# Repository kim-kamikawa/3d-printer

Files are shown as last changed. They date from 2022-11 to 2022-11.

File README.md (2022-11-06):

# 3D-Printer

## Overview

An Anet A8 3D printer was stripped of its controller board and its components connected to an Arduino Uno as shown in the following schematic.
Schematic

|Part ID|Part Name|Part Number||Part ID|Part Name|Part Number|
|---|---|---|---|---|---|---|
|C1|0.1uF|||U4|Stepper Driver|A4988|
|C2|0.1uF|||U5|Stepper Driver|A4988|
|C3|0.1uF|||U6|X-Axis Stepper|42SHDC3025-24B|
|C4|0.1uF|||U7|Y-Axis Stepper|42SHDC3025-24B|
|C5|0.1uF|||U8|Z-Axis Stepper|42SHDC3025-24B|
|C6|100uF|||U9|Z-Axis Stepper|42SHDC3025-24B|
|C7|100uF|||U10|Extruder Stepper|42SHDC3025-24B|
|C8|100uF|||U11|X-Min Stop|10T85|
|C9|100uF|||U12|Y-Min Stop|10T85|
|C10|10uF|||U13|Z-Min Stop|10T85|
|M1|IRF520|||U14|Power Module|BIQU-3D0109|
|R1|100k|||U15|Hot End|ANET-0029|
|U1|Arduino Uno|Arduino-A000066||U16|Thermistor|NTC 3960 100k|
|U2|Stepper Driver|A4988||U17|USB to Serial|OSEPP FTD-01|
|U3|Stepper Driver|A4988|

A STL file (cube.stl) was created of a 1.25-inch cube with 0.125-inch walls and a 1-inch by 0.125-inch opening on top. The STL was converted into g-code (cube.gcode) using Cura.

Knowing Repetier Host would be used to stream the g-code from a PC to the Arduino Uno, code was created for the Arduino Uno to receive g-code through its USART and parse the subset of g-code commands found in the g-code file.

The following g-codes from the file were implemented: G0 (rapid linear move), G1 (linear move), G28 (move to origin), and M109 (set extruder temperature and wait). In addition, M105 (get extruder temperature) was implemented to display the extruder’s temperature in Repetier Host. 

The following settings are hard-coded: units are in millimeters, all positioning is absolute, fans are always on and feed rate is constant. Since feed rate is constant, parameter ‘F’ is not used and, G0 and G1 are executed in the same manner. Additional restrictions to G0 and G1 functionalities are as follows: the length of filament to extrude is calculated (one pulse to the extruder stepper motor for every thirty pulses to the movement stepper motors), filament is only extruded if there is movement and the extruder direction is never reversed. Since the extruder direction is never reversed, the last two G1 lines in cube.gcode were commented out.

For M105 and M109, a one second timer triggers the ADC conversion of the thermistor voltage and the temperature is determined using the calculations found at https://www.allaboutcircuits.com/projects/measuring-temperature-with-an-ntc-thermistor/.

Controller_Hardware
Anet_A8
3D_Object

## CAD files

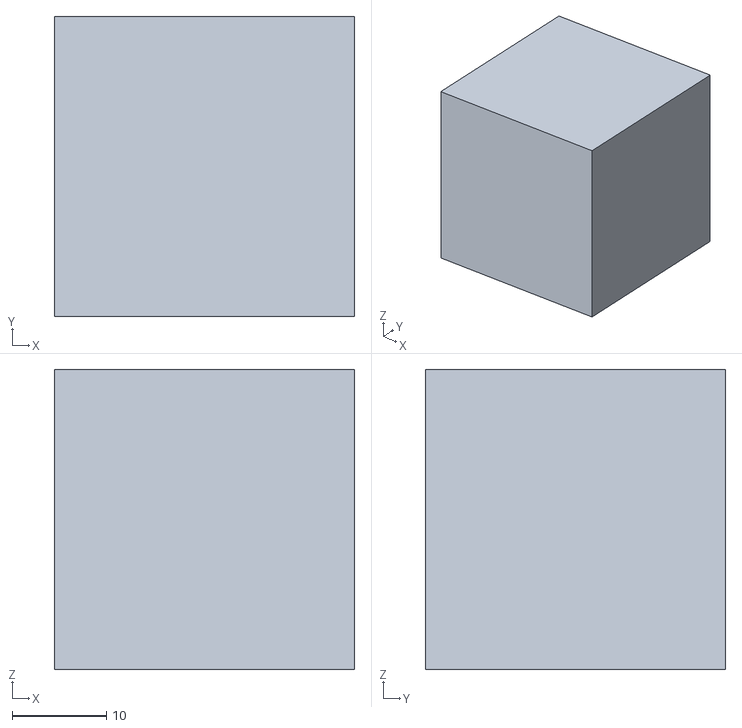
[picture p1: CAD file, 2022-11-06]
cube.STL
31.8 x 31.8 x 31.8

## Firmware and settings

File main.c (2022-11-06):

// Kim Lopez
// Embedded Controller Hardware Design
// ECE - 40001
// Final Project - 3D Printer
// 08-31-2018
  
#define F_CPU                   16000000
#define BAUD                    9600

#include <avr/io.h>
#include <avr/interrupt.h>
#include <util/delay.h>
#include <math.h>

#define BALANCE_RESISTOR 		100500.0
#define MAX_ADC 				1023.0
#define BETA 					3950.0
#define KELVIN_CONSTANT			273.15
#define ROOM_TEMP 				(25 + KELVIN_CONSTANT)
#define RESISTANCE_AT_ROOM_TEMP 100000

#define HOTEND_PWM_PIN          PB3

#define X_DIR_PIN               PD2   
#define X_STEP_PIN              PD3
#define X_HOME_PIN              PD4  
#define X_STEPS_PER_MM          100
 
#define Y_DIR_PIN               PD5 
#define Y_STEP_PIN              PD6
#define Y_HOME_PIN              PD7  
#define Y_STEPS_PER_MM          100

#define Z_DIR_PIN               PB0  
#define Z_STEP_PIN              PB1
#define Z_HOME_PIN              PB2   
#define Z_STEPS_PER_MM          400

#define E_DIR_PIN               PB4
#define E_STEP_PIN              PB5

#define PULSE_DURATION			200

struct Gcode {
	char letter;
	uint8_t number;
	uint8_t hasX;
	double x;
	uint8_t hasY;
	double y;
	uint8_t hasZ;
	double z;
	uint8_t hasE;
};

struct Position {
	double x;
	double y;
	double z;
};

volatile double hotEndTemperature = 0;
double hotEndSetting = 0;
int hotEndCounter = 0;

/*** SERIAL ***/

void initUSART() {
	// set baud rate
	unsigned int ubrr = F_CPU/16/BAUD-1;
	UBRR0H = (uint8_t)(ubrr>>8);
	UBRR0L = (uint8_t) ubrr;
	// enable receiver and transmitter
	UCSR0B |= (1<<RXEN0) | (1<<TXEN0);
	// 8-bit, no parity, 1 stop bit
	UCSR0C |= (1<<UCSZ01) | (1<<UCSZ00);   
}

uint8_t receiveUSART(void) {
	// wait for data to receive
	while (!(UCSR0A & (1<<RXC0)))
		;
	// return received byte
	return UDR0;
}

void transmitUSART(uint8_t data) {
	// wait for empty transmit buffer
	while (!(UCSR0A & (1<<UDRE0)))
		;
	// put data into buffer
	UDR0 = data;
}

/*** ADC ***/

void initADC() {
	/* initialize one second timer */
	// set CTC mode to match OCR1A (mode 4)
	TCCR1A = 0x0;
	TCCR1B = (1 << WGM12);
	// set prescaler to 1024 
	// => 16MHz/1024 = 15625Hz
	TCCR1B |= (1<<CS12) | (1<<CS10);
	// set compare match
	// => 15625 ticks = 1 second
	OCR1A = 15625;
	// initialize counter
	TCNT1 = 0;
	// enable Timer/Counter1 Compare Match A Interrupt
	TIMSK1 |= (1 << OCIE1A);

	/* initialize ADC */
	// set channel to pin A0 (PC0)
	// set voltage reference to AVcc
	ADMUX = (1<<REFS0);
	// set prescaler to 128
	// => 16MHz/128 = 125kHz
	// => ADC requires 50kHz-200kHz 
	ADCSRA |= (1<<ADPS2) | (1<<ADPS1) | (1<<ADPS0);
	// enable ADC interrupt
	ADCSRA |= (1<<ADIE);
	// turn off digital circuitry on A0
	DIDR0 |= (1<<ADC0D);
	// enable ADC
	ADCSRA |= (1<<ADEN);
	
	// enable global interrupt
	sei();
}

ISR(TIMER1_COMPA_vect) {
    // start ADC conversion
	ADCSRA |= (1<<ADSC);
}

ISR(ADC_vect) {
	// determine temperature of thermistor
	// https://www.allaboutcircuits.com/projects/measuring-temperature-with-an-ntc-thermistor/
	double rThermistor = BALANCE_RESISTOR * ((MAX_ADC / ADC) - 1);
	double tKelvin = (BETA * ROOM_TEMP) / (BETA + (ROOM_TEMP * log(rThermistor / RESISTANCE_AT_ROOM_TEMP)));
	hotEndTemperature = tKelvin - KELVIN_CONSTANT;
}

/*** HOT END ***/

void initHotEnd() {	
	/* initialize hot end PWM */
	// set pin 11 (PB3 & OC2A) as output
	DDRB |= (1<<HOTEND_PWM_PIN);
	// set fast PWM, top = 0xFF
	TCCR2A = (1<<WGM21) | (1<<WGM20);
	// set OC2A on compare match, clear OC2A at bottom
	TCCR2A |= (1<<COM2A1) | (1<<COM2A0);
	// set prescaler to 128
	// => 16MHz/128/256 = PWM frequency
	TCCR2B = (1<<CS22) | (1<<CS20);
	// set compare match
	// => 255 = 0% duty cycle (compare match ignored)
	// => 0 = 100% duty cycle
	OCR2A = 255;
	// initialize counter
	TCNT2 = 0;
}

/*** HOME SWITCHES and STEPPER MOTORS **/

void initHomeSwitches() {
	// home switches: set for input and pull-up resistor
	PORTD |= (1<<X_HOME_PIN) | (1<<Y_HOME_PIN);
	PORTB |= (1<<Z_HOME_PIN);
}

void initSteppers() {
	// set all steppers for output
	DDRD |= (1<<X_DIR_PIN) | (1<<X_STEP_PIN) | (1<<Y_DIR_PIN) | (1<<Y_STEP_PIN);
	DDRB |= (1<<Z_DIR_PIN) | (1<<Z_STEP_PIN) | (1<<E_DIR_PIN) | (1<<E_STEP_PIN);
	// set direction of stepper to extrude
	PORTB |= (1<<E_DIR_PIN);
}

/*** PARSING ***/

uint8_t getNumber(double *value) {
	
	uint8_t data;
	int num = 0;
	uint8_t multiplier = 1;
	double decimal = 0.0;
	uint8_t place = 0;
	
	// get integer part
	do {
		data = receiveUSART();
		switch (data) {
			case '+':
				break;
			case '-':
				multiplier = -1;
				break;
			case '0': case '1': case '2': case '3': case '4':
			case '5': case '6': case '7': case '8': case '9':
			    num = (num*10) + (data-'0');
				break;
			default:
				break;
		}
	} while (!((data == ' ') || (data == '.')));
	num *= multiplier;
	// get decimal part
	if (data == '.') {
		do {
			data = receiveUSART();
			switch (data) {
				case '0': case '1': case '2': case '3': case '4':
				case '5': case '6': case '7': case '8': case '9':
					decimal = (decimal*10.0) + (data-'0');
					place++;
					break;
				default:
					break;
			}
		} while (data != ' ');
		for (uint8_t x=0; x<place; x++)
			decimal *= 0.1;
	}
	
	*value = num + decimal;
	return data;
}

struct Gcode getCommand() {
	uint8_t data;
	struct Gcode command = {' ', 0, 0, 0.0, 0, 0.0, 0, 0.0, 0};
	
	// ignore line numbers
	do {
		
		data = receiveUSART(); 
	} while (data != ' ');
	
	// get letter
	data = receiveUSART();
		
	switch (data) {
		case 'G':
			data = receiveUSART();
			command.letter = 'G';			
			// get number
			switch (data) {
				case '0':
				case '1':
					command.number = 0;
					// G0: rapid linear move & G1: linear move
					data = receiveUSART();
					do {
						data = receiveUSART();
						
						// get parameters
						switch (data) {
							case 'X':
								// x coordinate in mm
								command.hasX = 1;
								data = getNumber(&(command.x));
								break;
							case 'Y':
								// y coordinate in mm
								command.hasY = 1;
								data = getNumber(&(command.y));
								break;
							case 'Z':
								// z coordinate in mm
								command.hasZ = 1;
								data = getNumber(&(command.z));
								break;
							case 'E':
								// e coordinate in mm
								command.hasE = 1;
								do {
									data = receiveUSART();
								} while (data != ' ');
								break;
							case 'F':
								// feedrate in mm per minute
								do {
									data = receiveUSART();
								} while (data != ' ');
								break;
							default:
								break;
						}
					} while (data != '*');
					break;
				case '2':
					data = receiveUSART();
					switch (data) {
						case '8':
							command.number = 28;
							// G28: move to origin
							data = receiveUSART();
							do {
								data = receiveUSART();
						
								// get parameters
								switch (data) {
									case 'X':
										// x coordinate in mm
										command.hasX = 1;
										data = getNumber(&(command.x));
										break;
									case 'Y':
										// y coordinate in mm
										command.hasY = 1;
										data = getNumber(&(command.y));
										break;
									case 'Z':
										// z coordinate in mm
										command.hasZ = 1;
										data = getNumber(&(command.z));
										break;
									default:
										break;
								}
							} while (data != '*');
							break;
						default:
							break;
					}
					break;
				default:
					break;
			}
			break; // 'G'
		case 'M':
			data = receiveUSART();
			command.letter = 'M';			
			// get number
			switch (data) {
				case '1':
					data = receiveUSART();
					switch (data) {
						case '0':
							data = receiveUSART();
							switch (data) {
								case '5':
									command.number = 105;
									// M105: get extruder temperature
									break;
								case '9':
									command.number = 109;
									// M109: set extruder temperature and wait
									data = receiveUSART();
									do {
										data = receiveUSART();
										switch (data) {
											case 'T':
												// temperature sensor number
												do {
													data = receiveUSART();
												} while (data != ' ');
												break;
											case 'S':
												// temperature value
												data = getNumber(&(hotEndSetting));
												break;
											default:
												break;
										}
									} while (data != '*');
									break;
								default:
									break;
							}
							break;
						default:
							break;
					}
					break;
				default:
					break;
			}
			break;
		default:
			break;
	}

	// ignore checksum
	do {
		data = receiveUSART(); 
	} while (!((data == '\r') || (data == '\n')));
	
	return command;
}
	
void sendOk() {
	// acknowledge receipt of command
	transmitUSART('o');
	transmitUSART('k');
	transmitUSART('\n');
}

/*** GCODE COMMANDS ***/

struct Position goLinear(struct Gcode gcode, struct Position currentPosition) {
	
	// G0: rapid linear move & G1: linear move
	int xSteps=0, ySteps=0, zSteps=0;
	struct Position position = currentPosition;

	if (gcode.hasX) {
		// compute steps
		xSteps = round((gcode.x - currentPosition.x) * X_STEPS_PER_MM);
		// set direction
		if (xSteps>0) {
			// go right
			PORTD |= (1<<X_DIR_PIN);
		}
		else {
			// go left
			PORTD &= ~(1<<X_DIR_PIN);
			xSteps *= -1;
		}
		// set ending position
		position.x = gcode.x;
	}
	if (gcode.hasY) {
		// compute steps
		ySteps = round((gcode.y - currentPosition.y) * Y_STEPS_PER_MM);
		// set direction
		if (ySteps>0) {
			// go front
			PORTD |= (1<<Y_DIR_PIN);
		}
		else {
			// go back
			PORTD &= ~(1<<Y_DIR_PIN);
			ySteps *= -1;
		}
		// set ending position
		position.y = gcode.y;
	}
	if (gcode.hasZ) {
		// compute steps
		zSteps = round((gcode.z - currentPosition.z) * Z_STEPS_PER_MM);
		// set direction
		if (zSteps>0) {
			// go up
			PORTB &= ~(1<<Z_DIR_PIN);
		}
		else {
			// go down
			PORTB |= (1<<Z_DIR_PIN);
			zSteps *= -1;
		}
		// set ending position
		position.z = gcode.z;
	}

	while (xSteps || ySteps || zSteps) {
		if (xSteps) {
			// send pulse to X-axis stepper
			PORTD |= (1<<X_STEP_PIN);
			xSteps--;
		}
		if (ySteps) {
			// send pulse to Y-axis stepper
			PORTD |= (1<<Y_STEP_PIN);
			ySteps--;
		}
		if (zSteps) {
			// send pulse to Z-axis steppers
			PORTB |= (1<<Z_STEP_PIN);
			zSteps--;
		}
		
		if (gcode.hasE) {
			// send pulse to extruder stepper
			// one extruder pulse for every 30 movement pulses
			if (hotEndCounter == 0) {
				PORTB |= (1<<E_STEP_PIN);
				hotEndCounter++;
			}
			else {
				if (hotEndCounter == 29)
					hotEndCounter = 0;
				else
					hotEndCounter++;
			}
		}
		
		// pulse duration
		_delay_us(PULSE_DURATION);
		
		// stop pulse
		PORTD &= ~(1<<X_STEP_PIN);
		PORTD &= ~(1<<Y_STEP_PIN);
		PORTB &= ~(1<<Z_STEP_PIN);	
		PORTB &= ~(1<<E_STEP_PIN);		
		
		// stop pulse duration
		_delay_us(PULSE_DURATION);
	} 
	
	return position;
}

struct Position goHome(struct Gcode gcode, struct Position currentPosition) {
	
	// G28: move to origin
	struct Position position = currentPosition;
	
	if (gcode.hasX) {
		// move X-axis stepper home
		PORTD &= ~(1<<X_DIR_PIN);
		while (bit_is_set(PIND, X_HOME_PIN)) {
			PORTD |= (1<<X_STEP_PIN);
			_delay_us(PULSE_DURATION);
			PORTD &= ~(1<<X_STEP_PIN);
			_delay_us(PULSE_DURATION);
		}
		// move X-axis stepper to zero
		PORTD |= (1<<X_DIR_PIN);
		for (int x=0; x<33*100; x++) {
			PORTD |= (1<<X_STEP_PIN);
			_delay_us(PULSE_DURATION);
			PORTD &= ~(1<<X_STEP_PIN);
			_delay_us(PULSE_DURATION);
		}
		position.x = 0;
	}
	if (gcode.hasY) {
		// move Y-axis stepper home
		PORTD &= ~(1<<Y_DIR_PIN);
		while (bit_is_set(PIND, Y_HOME_PIN)) {
			PORTD |= (1<<Y_STEP_PIN);
			_delay_us(PULSE_DURATION);
			PORTD &= ~(1<<Y_STEP_PIN);
			_delay_us(PULSE_DURATION);
		} 
		// move Y-axis stepper to zero
		PORTD |= (1<<Y_DIR_PIN);
		for (int x=0; x<4*100; x++) {
			PORTD |= (1<<Y_STEP_PIN);
			_delay_us(PULSE_DURATION);
			PORTD &= ~(1<<Y_STEP_PIN);
			_delay_us(PULSE_DURATION);
		}
		position.y = 0;
	}
	if (gcode.hasZ) {
		// move Z-axis stepper home
		PORTB |= (1<<Z_DIR_PIN);
		while (bit_is_set(PINB, Z_HOME_PIN)) {
			PORTB |= (1<<Z_STEP_PIN);
			_delay_us(PULSE_DURATION);
			PORTB &= ~(1<<Z_STEP_PIN);
			_delay_us(PULSE_DURATION);
		}
		// home is Z-axis origin
		position.z = 0;
	}

	return position;
}

void sendHotEndTemperature() {
	// M105: get extruder temperature
	transmitUSART('T');
	transmitUSART(':');
	transmitUSART('0' + ((int)hotEndTemperature / 100)); 
	transmitUSART('0' + (((int)hotEndTemperature / 10) % 10));                   
	transmitUSART('0' + ((int)hotEndTemperature % 10));                             
	transmitUSART('\n');
}

void waitHotEndTemperature(struct Gcode gcode) {
	// M109: set extruder temperature and wait
	while (hotEndTemperature < hotEndSetting)
		// send hot end temperature to host
		sendHotEndTemperature();
}

/*** MAIN LOOP ***/

int main(void) {
	
	struct Gcode gcode;
	struct Position currentPosition = {0.0, 0.0, 0.0};

	// initialization
	initUSART();
	initADC();
	initHotEnd();
	initHomeSwitches();
	initSteppers();

	// main loop
	while (1) {

		gcode = getCommand();
		
		// maintain hot end temperature
		if (hotEndTemperature > (hotEndSetting))
			// PWM off
			OCR2A = 255;
			// PWM on
		else
			OCR2A = 64;

		switch (gcode.letter) {
			case 'G':
				switch (gcode.number) {
					case 0:
						// linear move
						currentPosition = goLinear(gcode, currentPosition);
						break;
					case 28:
						// home
						currentPosition = goHome(gcode, currentPosition);
						break;
					default:
						break;
				}
				break;
			case 'M':
				switch (gcode.number) {
					case 105:
						// send hot end temperature to host
						sendHotEndTemperature();
						break;
					case 109:
						// wait for hot end to meet temperature
						waitHotEndTemperature(gcode);
					default:
						break;
				}
				break;
			default:
				break;
		}
		// send acknowledgment to host
		sendOk();
	}                                                
	return 0;
}
